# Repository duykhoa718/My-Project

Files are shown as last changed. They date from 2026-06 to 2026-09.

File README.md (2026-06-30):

This is the workplace for designing a buck converter with 6.8V and 20A current max.
This circuit is used for serving the 12 servo Miuzel 20kg torque with a current load from 1-2A 
The purpose of using 12 servos is to design a 12 servo with enough power supply and connect it to the Jetson Orin Nano to control the movement
The input power source is only designed for a 5s LiPo battery.

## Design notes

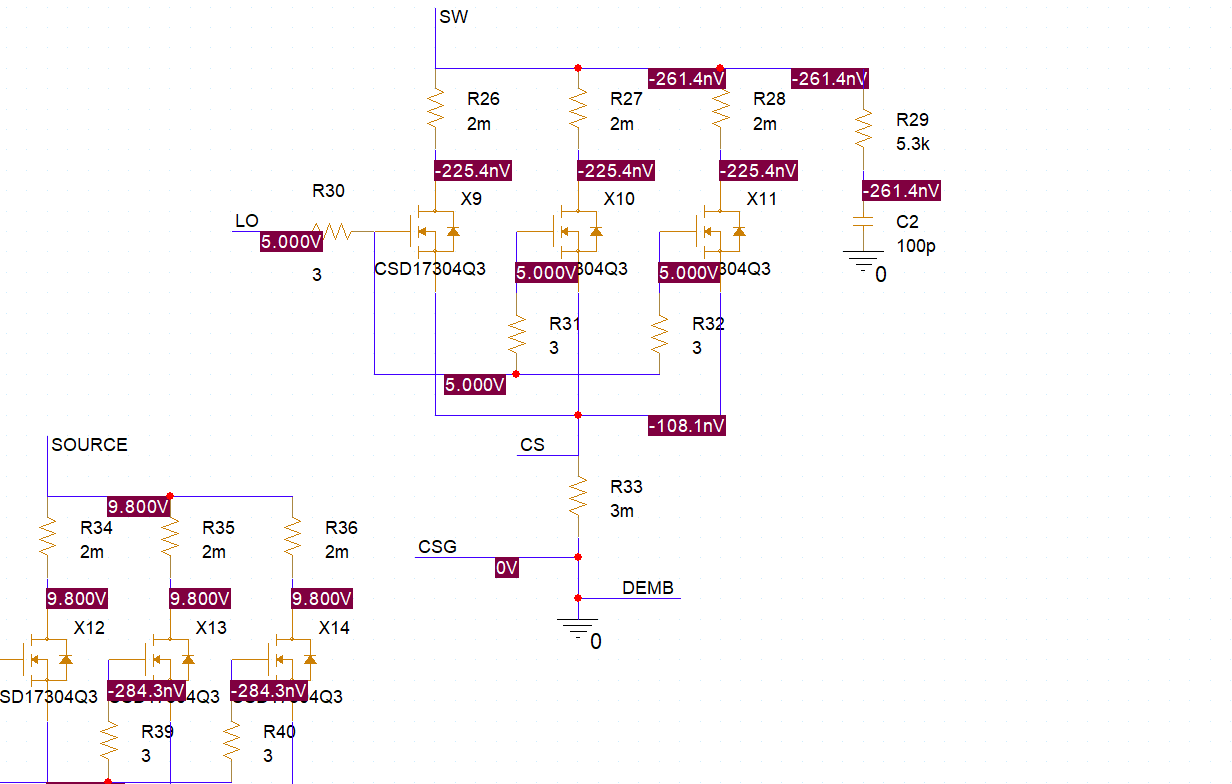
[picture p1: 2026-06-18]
Ai Sipder Bot Power System/PSpice And LTspice For Ti LM5116 Design Schematic/LM5116/LM5116.png

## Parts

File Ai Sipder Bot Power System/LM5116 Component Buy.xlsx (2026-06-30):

DigiKey - Shopping Cart
Index | Quantity | Part Number | Manufacturer Part Number | Description | Customer Reference | Available | Backorder | Unit Price | Extended Price USD
1 | 2 | 1276-1040-1-ND | CL10A225KO8NNNC | CAP CER 2.2UF 16V X5R 0603 |  | 2 | 0 | 0.1 | 0.20
2 | 10 | 296-27509-1-ND | CSD17304Q3 | MOSFET N-CH 30V 15A/56A 8VSON |  | 10 | 0 | 0.935 | 9.35
3 | 1 | 296-40599-1-ND | TLV1701AIDBVR | IC COMPARATOR 1 GEN PUR SOT23-5 |  | 1 | 0 | 1.16 | 1.16
4 | 1 | 5399-TL431CT-ND | TL431 | 2.5V~36V 2% 37V 100MA ADJUSTABLE |  | 1 | 0 | 0.1 | 0.10
5 | 10 | 1N5819HW-FDICT-ND | 1N5819HW-7-F | DIODE SCHOTTKY 40V 1A SOD123 |  | 10 | 0 | 0.178 | 1.78
6 | 10 | 490-14514-1-ND | GCM155R71H104KE02J | CAP CER 0.1UF 50V X7R 0402 |  | 10 | 0 | 0.034 | 0.34
7 | 1 | 399-C0603C824K4PACTUCT-ND | C0603C824K4PACTU | CAP CER 0.82UF 16V X5R 0603 |  | 1 | 0 | 0.26 | 0.26
8 | 1 | 399-A768EB107M1ELAS036CT-ND | A768EB107M1ELAS036 | CAP ALUM POLY 100UF 20% 25V SMD |  | 1 | 0 | 0.55 | 0.55
9 | 10 | 490-6113-1-ND | GRM0335C1H101JA01D | CAP CER 100PF 50V C0G/NP0 0201 |  | 10 | 0 | 0.014 | 0.14
10 | 2 | 553-3446-1-ND | PA4343.142NLT | FIXED IND 1.4UH 27A 2.6 MOHM SMD |  | 2 | 0 | 1.69 | 3.38
11 | 1 | 311-1.21KHRCT-ND | RC0603FR-071K21L | RES 1.21K OHM 1% 1/10W 0603 |  | 1 | 0 | 0.1 | 0.10
12 | 1 | 2019-RN73R1ETTP4811B25CT-ND | RN73R1ETTP4811B25 | RES 4.81K OHM 0.1% 1/16W 0402 |  | 1 | 0 | 0.1 | 0.10
13 | 1 | 311-226KHRCT-ND | RC0603FR-07226KL | RES 226K OHM 1% 1/10W 0603 |  | 1 | 0 | 0.1 | 0.10
14 | 1 | 490-6186-1-ND | GRM1555C1H100FA01D | CAP CER 10PF 50V C0G/NP0 0402 |  | 1 | 0 | 0.1 | 0.10
15 | 10 | 311-0.0JRCT-ND | RC0402JR-070RL | RES 0 OHM JUMPER 1/16W 0402 |  | 10 | 0 | 0.01 | 0.10
16 | 1 | 296-LM5155QDSSTQ1CT-ND | LM5155QDSSTQ1 | POWER MANAGEMENT |  | 1 | 0 | 3.6 | 3.60
17 | 1 | 296-TPS552892RYQRCT-ND | TPS552892RYQR | IC REG BUCK BOOST PROG 5A 21VQFN |  | 1 | 0 | 7.21 | 7.21
18 | 10 | 13-RC0402FR-073RLCT-ND | RC0402FR-073RL | RES 3 OHM 1% 1/16W 0402 |  | 10 | 0 | 0.026 | 0.26
19 | 1 | 1727-8643-1-ND | 2N7002NXAKR | MOSFET N-CH 60V 190MA TO236AB |  | 1 | 0 | 0.14 | 0.14
20 | 10 | 311-1.00MLRCT-ND | RC0402FR-071ML | RES 1M OHM 1% 1/16W 0402 |  | 10 | 0 | 0.021 | 0.21
21 | 10 | 399-C0603C105K4RACTUCT-ND | C0603C105K4RACTU | CAP CER 1UF 16V X7R 0603 |  | 10 | 0 | 0.054 | 0.54
22 | 1 | 2019-RN73R1JTTD5301B25CT-ND | RN73R1JTTD5301B25 | RES 5.3K OHM 0.1% 1/10W 0603 |  | 1 | 0 | 0.1 | 0.10
23 | 2 | 2019-RN73R1ETTP5831B25CT-ND | RN73R1ETTP5831B25 | RES 5.83K OHM 0.1% 1/16W 0402 |  | 2 | 0 | 0.1 | 0.20
24 | 5 | 5923-0678H9300-02CT-ND | 0678H9300-02 | FUSE BRD MT 30A 250VAC 125VDC |  | 5 | 0 | 1.026 | 5.13
25 | 1 | 1276-1244-1-ND | CL21A475KAQNNNE | CAP CER 4.7UF 25V X5R 0805 |  | 1 | 0 | 0.11 | 0.11
26 | 4 | 399-A768MS157M1HLAE024CT-ND | A768MS157M1HLAE024 | CAP ALUM POLY 150UF 20% 50V SMD |  | 4 | 0 | 1.14 | 4.56
27 | 1 | 311-2KLRCT-ND | RC0402FR-072KL | RES 2K OHM 1% 1/16W 0402 |  | 1 | 0 | 0.1 | 0.10
28 | 1 | P140HCT-ND | ERJ-3EKF1400V | RES SMD 140 OHM 1% 1/10W 0603 |  | 1 | 0 | 0.1 | 0.10
29 | 1 | 846-SML-D12U8WT86CT-ND | SML-D12U8WT86 | LED RED DIFFUSED 0603 SMD |  | 1 | 0 | 0.2 | 0.20
30 | 1 | 448-IQDH29NE2LM5CGATMA1CT-ND | IQDH29NE2LM5CGATMA1 | OPTIMOS 6 POWER-TRANSISTOR |  | 1 | 0 | 3.75 | 3.75
31 | 1 | 738-CSSU2512FT3L00CT-ND | CSSU2512FT3L00 | RES SHUNT, 2512, 0.003 OHM, 1%, |  | 1 | 0 | 1.14 | 1.14
32 | 1 | RG16P5.6KBCT-ND | RG1608P-562-B-T5 | RES SMD 5.6K OHM 0.1% 1/10W 0603 |  | 1 | 0 | 0.11 | 0.11
33 | 12 | 732-5316-ND | 61300311121 | CONN HEADER VERT 3POS 2.54MM |  | 12 | 0 | 0.113 | 1.36
34 | 12 | 2057-PH1-01-UA-ND | PH1-01-UA | CONN HEADER VERT 1POS 2.54MM |  | 12 | 0 | 0.029 | 0.35
35 | 1 | LM5116MHX/NOPBCT-ND | LM5116MHX/NOPB | IC REG CTRLR BUCK 20TSSOP |  | 1 | 0 | 6.35 | 6.35
36 | 1 | EG2355-ND | 100SP1T1B4M2QE | SWITCH TOGGLE SPDT 5A 120V |  | 1 | 0 | 2.93 | 2.93
37 | 1 | 399-A783MW687M1VLAS011CT-ND | A783MW687M1VLAS011 | CAP ALU HYBRID 125C 35V 680UF |  | 1 | 0 | 1.86 | 1.86
38 | 1 | 445-5599-1-ND | CGA2B2C0G1H181J050BA | CAP CER 180PF 50V C0G 0402 |  | 1 | 0 | 0.1 | 0.10
39 | 1 | 478-KGM21NR71H333JTCT-ND | KGM21NR71H333JT | CAP CER 0.033UF 50V X7R 0805 |  | 1 | 0 | 0.21 | 0.21
40 | 1 | 541-22.6KLCT-ND | CRCW040222K6FKED | RES 22.6K OHM 1% 1/16W 0402 |  | 1 | 0 | 0.1 | 0.10
41 | 1 | P2.49KDBCT-ND | ERA-3AEB2491V | RES SMD 2.49KOHM 0.1% 1/10W 0603 |  | 1 | 0 | 0.1 | 0.10

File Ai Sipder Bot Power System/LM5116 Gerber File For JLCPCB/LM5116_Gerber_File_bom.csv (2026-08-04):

Designator | Footprint | Quantity | Value | LCSC Part #
C10, C6, C7 | 0603 | 3 | 1u
C11, C14 | CP_Radial_D10.0mm_P5.00mm | 2 | 2200u
C15, C16, C17, C18, C22, C23, C24 | 0603 | 7 | 2.2u
C19, C21, C8 | 0603 | 3 | 100p
C2 | 0603 | 1 | 180p
C20 | 0603 | 1 | 10p
C3 | 1206 | 1 | 33n
C4 | CP_Radial_D10.0mm_P5.00mm | 1 | 1000u
C5 | 0805 | 1 | 4.7u
C9 | 0603 | 1 | 820n
CR1 | CR_LT27A-7_DIO | 1 | DFLT27A-7
CR2 | SMB_DIO | 1 | SMBJ7.0CA-13-F
D1, D2, D3 | SOD3715X145N | 3 | 1N5819HW-7-F
D4 | 0603 | 1 | LED
F1 | FUSC9830X318N | 1 | 0678H9300-02
J1, J10, J11, J12, J2, J3, J4, J5, J6, J7, J8, J9 | WURTH_61300411121 | 12 | 61300411121
J14 | AMASS_XT60-M | 1 | XT60-M
J15 | CUI_TB002V-500-02BE | 1 | TB002V-500-02BE
L1, L2 | L_Pulse_PA4341 | 2 | 1.38u
Q1, Q2, Q3, Q4 | DQG0008A | 4 | CSD17304Q3
Q5 | SOT-23_Handsoldering | 1 | 2N7002
Q6 | IFX-PG-TTFN-9-2-V | 1 | IQDH29NE2LM5CG
R1 | 0402 | 1 | 0
R10 | 0603 | 1 | 226k
R11, R12, R14, R15 | 0603 | 4 | 3
R13, R22 | 0603 | 2 | 5.83k
R17 | 2512 | 1 | 3m
R19, R21, R23, R24, R25, R26, R27 | 0603 | 7 | 10k
R2 | 0805 | 1 | 22.6k
R20 | 0805 | 1 | 4.81k
R3 | 0805 | 1 | 2.49k
R4 | 0402 | 1 | 1Meg
R5 | 0603 | 1 | 5.3k
R6 | 0603 | 1 | 330
R7 | 0603 | 1 | 2k
R8 | 0603 | 1 | 5.6k
R9 | 0603 | 1 | 1.21k
SW1 | SW_1218_EWI | 1 | EG1218
U1 | MXA20A_TEX-M | 1 | LM25116MHX/NOPB
U2 | SOT95P280X145-5N | 1 | TLV1701AIDBVR
U3 | SOT-23_Handsoldering | 1 | TL431DBZ

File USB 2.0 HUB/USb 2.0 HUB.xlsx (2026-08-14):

DigiKey - Shopping Cart
Index | Quantity | Part Number | Manufacturer Part Number | Description | Unit of Measure | Customer Reference | Available | Backorder | Unit Price | Extended Price USD
1 | 1 | USB2512BT/M2CT-ND | USB2512BT/M2 | IC HUB CTLR 2PORT USB 2.0 HS 36S |  |  | 1 | 0 | 1.9 | 1.90
2 | 2 | 2057-USB-A-S-VT-ND | USB-A-S-VT | USB TYPE A SINGLE VERTICAL |  |  | 2 | 0 | 0.48 | 0.96
3 | 1 | 2073-USB4110-GF-A-1-ND | USB4110-GF-A | CONN RCP USB2.0 TYP C 24P SMD RA |  |  | 1 | 0 | 1.27 | 1.27
4 | 1 | SER3635CT-ND | TSX-3225 24.0000MF15X-AC3 | CRYSTAL 24.0000MHZ 9PF SMD |  |  | 1 | 0 | 0.87 | 0.87
5 | 2 | 490-3113-1-ND | GJM1555C1H100JB01D | CAP CER 10PF 50V C0G/NP0 0402 |  |  | 2 | 0 | 0.13 | 0.26
6 | 10 | 1934-1472-1-ND | 2508051217Y6 | FERRITE BEAD 120 OHM 0805 1LN |  |  | 10 | 0 | 0.092 | 0.92
7 | 1 | AZ1117CH-3.3TRG1DICT-ND | AZ1117CH-3.3TRG1 | IC REG LINEAR 3.3V 1A SOT-223-3 |  |  | 1 | 0 | 0.19 | 0.19
8 | 1 | 296-31979-1-ND | TPS2064DGNR | IC PWR SWITCH N-CHAN 1:2 8MSOP |  |  | 1 | 0 | 2.45 | 2.45
9 | 3 | NUP4114UPXV6T2GOSCT-ND | NUP4114UPXV6T2G | TVS DIODE 5.5VWM 10VC SOT563 |  |  | 3 | 0 | 0.88 | 2.64
10 | 10 | 311-634HRCT-ND | RC0603FR-07634RL | RES 634 OHM 1% 1/10W 0603 |  |  | 10 | 0 | 0.025 | 0.25
11 | 10 | 541-1.00KHCT-ND | CRCW06031K00FKEA | RES SMD 1K OHM 1% 1/8W 0603 |  |  | 10 | 0 | 0.032 | 0.32
12 | 10 | 541-100KHCT-ND | CRCW0603100KFKEA | RES SMD 100K OHM 1% 1/8W 0603 |  |  | 10 | 0 | 0.032 | 0.32
13 | 10 | 311-5.10KHRCT-ND | RC0603FR-075K1L | RES 5.1K OHM 1% 1/10W 0603 |  |  | 10 | 0 | 0.027 | 0.27
14 | 10 | 311-12.0KHRCT-ND | RC0603FR-0712KL | RES 12K OHM 1% 1/10W 0603 |  |  | 10 | 0 | 0.025 | 0.25
15 | 10 | 399-C0603C100J5GACTUCT-ND | C0603C100J5GACTU | CAP CER 10PF 50V C0G/NP0 0603 |  |  | 10 | 0 | 0.091 | 0.91
16 | 1 | 1276-1065-1-ND | CL21A475KOFNNNE | CAP CER 4.7UF 16V X5R 0805 |  |  | 1 | 0 | 0.11 | 0.11
17 | 1 | 587-3246-1-ND | TMK316BBJ226ML-T | CAP CER 22UF 25V X5R 1206 |  |  | 1 | 0 | 0.44 | 0.44
18 | 2 | 399-A768MS157M1HLAE024CT-ND | A768MS157M1HLAE024 | CAP ALUM POLY 150UF 20% 50V SMD |  |  | 2 | 0 | 1.17 | 2.34
19 | 20 | 445-7456-1-ND | C1608X5R1H104K080AA | CAP CER 0.1UF 50V X5R 0603 |  |  | 20 | 0 | 0.057 | 1.14
20 | 3 | 160-1423-1-ND | LTST-C171GKT | LED GREEN CLEAR CHIP SMD |  |  | 3 | 0 | 0.15 | 0.45
21 | 10 | 399-C0402C103K5RACTUCT-ND | C0402C103K5RACTU | CAP CER 10000PF 50V X7R 0402 |  |  | 10 | 0 | 0.037 | 0.37

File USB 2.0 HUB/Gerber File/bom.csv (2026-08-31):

Designator | Footprint | Quantity | Value | LCSC Part #
C1, C2 | 0402 | 2 | 10p
C10, C4 | 0805 | 2 | 4.7u
C11, C13, C14, C5, C6, C8 | 0805 | 6 | 0.1u
C12 | 1206 | 1 | 22u
C15, C3 | 0603 | 2 | 2.2u
C16 | 0603 | 1 | 1u
C17, C18, C19, C20, C23, C24 | 0603 | 6 | 0.1u
C21, C22 | 0402 | 2 | 10n
C7, C9 | CAP_A768MS_KEM | 2 | 150u
D1, D2, D3 | 0805 | 3 | LED
D4, D5, D6 | SOT95P275X110-6N | 3 | NUP4114HMR6T1G
J1, J2 | CONN_USB-A-S-VT_ADM | 2 | USB-A-S-VT
J3 | GCT_USB4110GFA | 1 | USB4110GFA
L1, L2 | IND_25_0805_FRT | 2 | 2508051217Y6
R1 | 0603 | 1 | 634
R10, R7, R8, R9 | 0603 | 4 | 330
R11, R12, R14, R15, R18, R19, R3, R4 | 0603 | 8 | 100k
R13 | 0402 | 1 | NP_1M
R16 | 0603 | 1 | 12k
R2 | 0603 | 1 | 1k
R5, R6 | 0603 | 2 | 5.1k
U1 | 36SQFN-3706-6X6B_MCH | 1 | USB2512BT/M2
U3 | SOT-223_DIO | 1 | AZ1117CH-3.3TRG1
U4 | DGN8_1P89X1P57 | 1 | TPS2064DGNR
Y1 | OSCCC320X250X60 | 1 | TSX-322524.0000MF15X-AC3

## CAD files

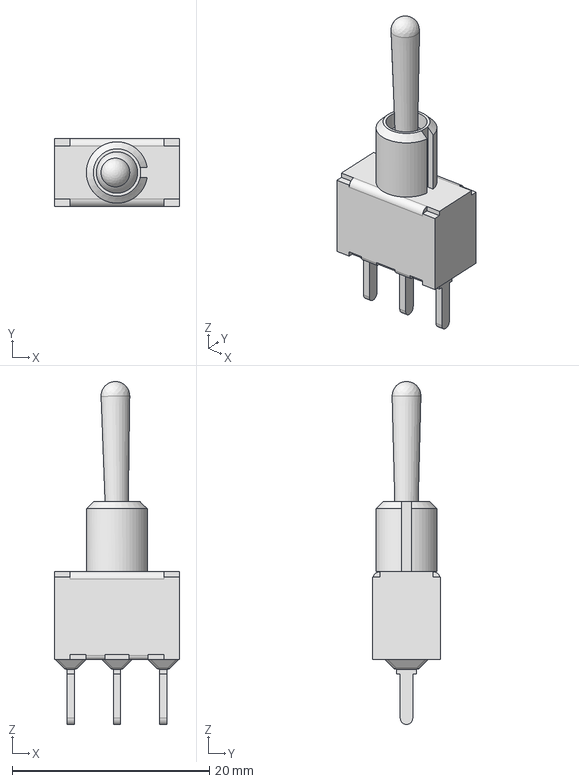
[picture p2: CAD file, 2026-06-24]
Ai Sipder Bot Power System/LM5116 Component File/100SP1T1B4M2QE/100SP1T1B4M2QE.step
12.7 x 6.86 x 34.8 mm

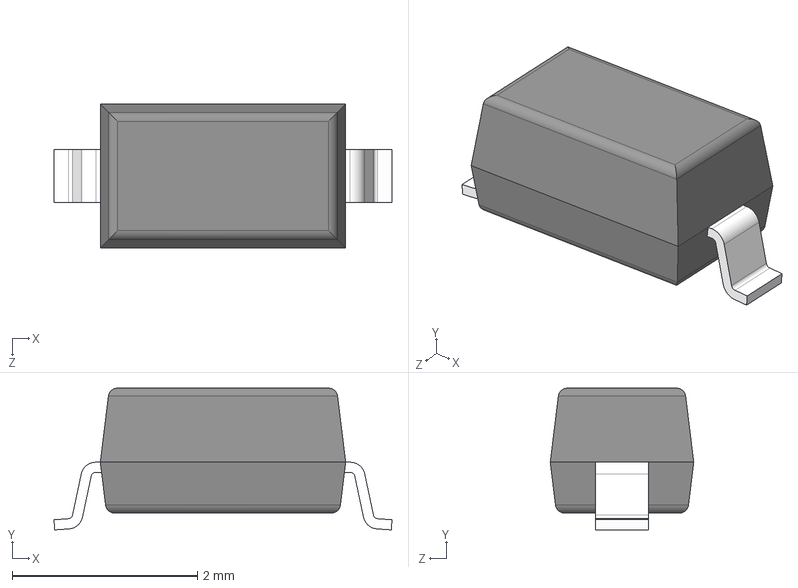
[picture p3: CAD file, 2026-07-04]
Ai Sipder Bot Power System/LM5116 Component File/1N5819HW_7_F/1N5819HW-7-F.step
3.65 x 1.53 x 1.55 mm

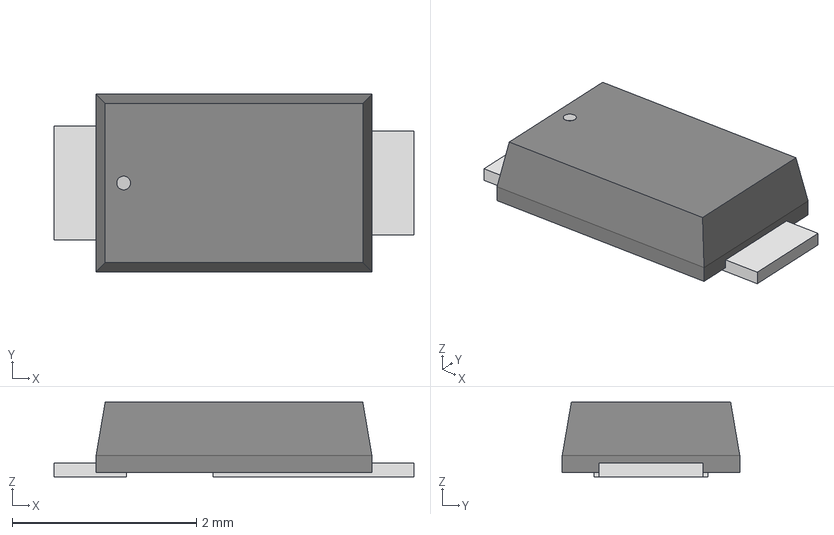
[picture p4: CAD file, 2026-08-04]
Ai Sipder Bot Power System/LM5116 Component File/DFLT27A_7/CR_LT27A-7_DIO.step
3.91 x 1.93 x 0.815 mm

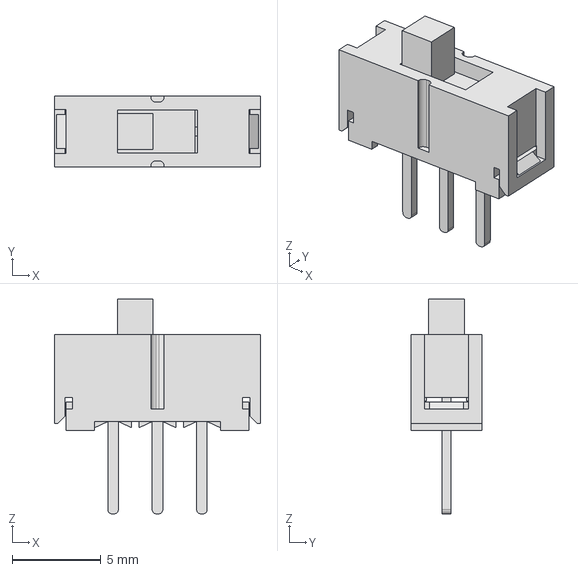
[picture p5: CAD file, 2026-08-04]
Ai Sipder Bot Power System/LM5116 Component File/EG1218/KiCADv6/EG1218.STEP
11.6 x 4.00 x 12.1 mm

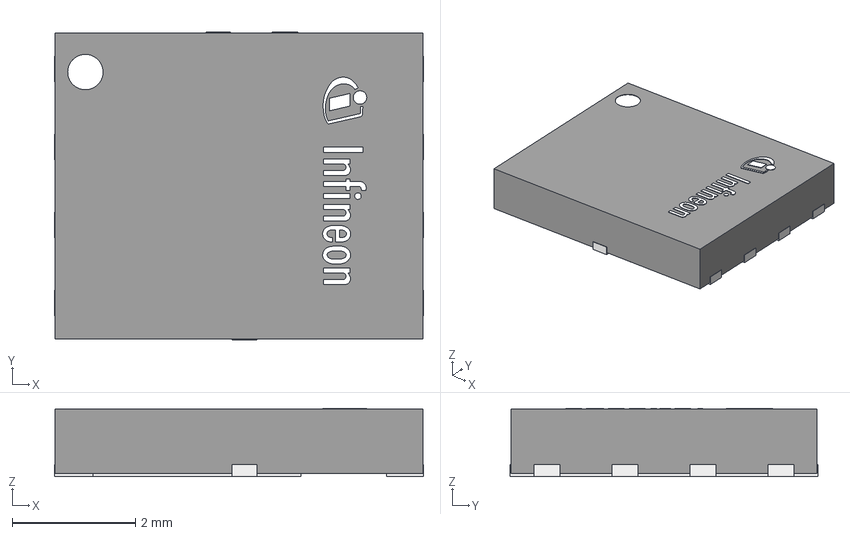
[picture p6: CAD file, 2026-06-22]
Ai Sipder Bot Power System/LM5116 Component File/IQDH29NE2LM5CGATMA1/PG-TTFN-9-2_Z8B00203958_V01_3D.stp
6.00 x 5.00 x 1.11 mm

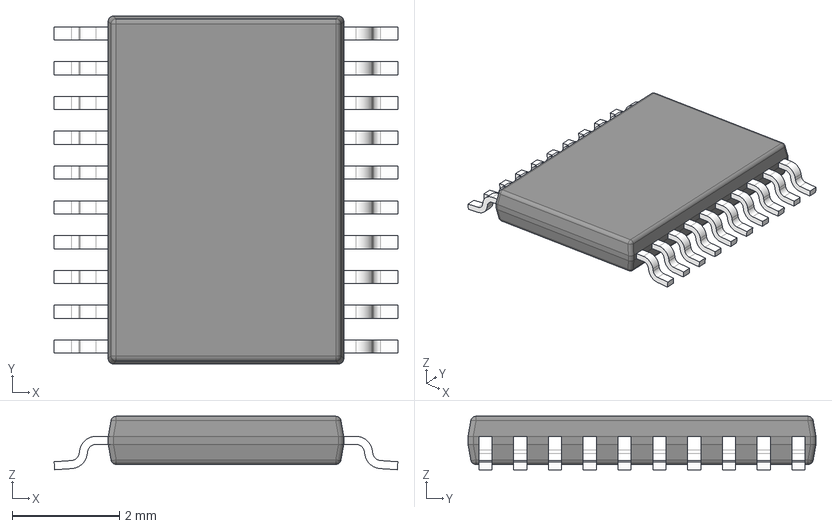
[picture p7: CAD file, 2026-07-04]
Ai Sipder Bot Power System/LM5116 Component File/LM25116MHX_NOPB/PWP0020A.stp
6.42 x 6.50 x 1.00 mm
BODY-SO
LEAD-SO x 20
THERMALPAD-SO
PIN1-ID

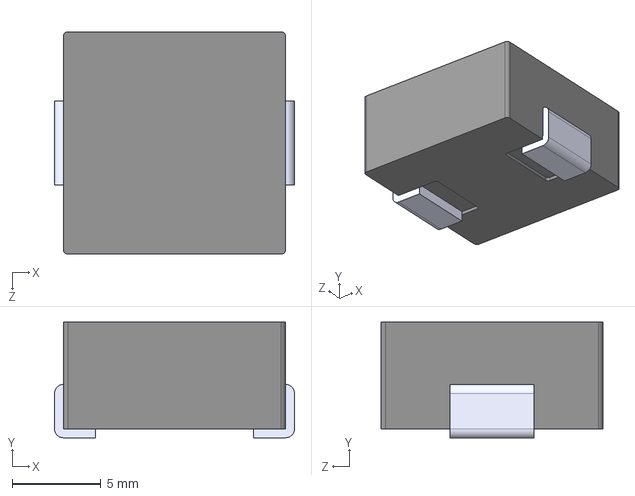
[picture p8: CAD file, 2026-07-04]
Ai Sipder Bot Power System/LM5116 Component File/PA4343_142NLT/PA4343.142NLT.STEP
13.5 x 6.50 x 12.5 mm

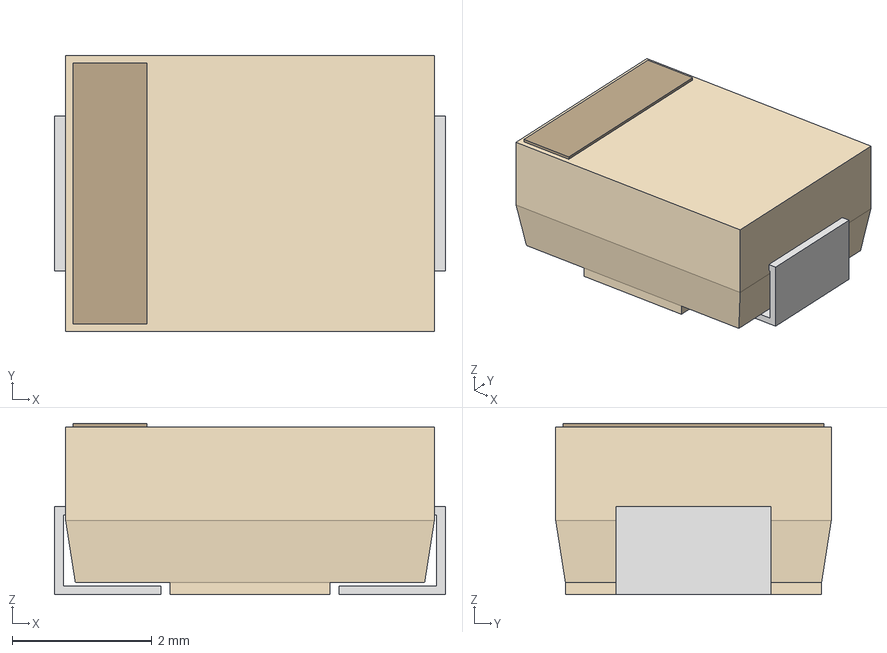
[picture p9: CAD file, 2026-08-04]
Ai Sipder Bot Power System/LM5116 Component File/SMBJ7_0CA_13_F/SMB_DIO.step
5.59 x 3.94 x 2.45 mm

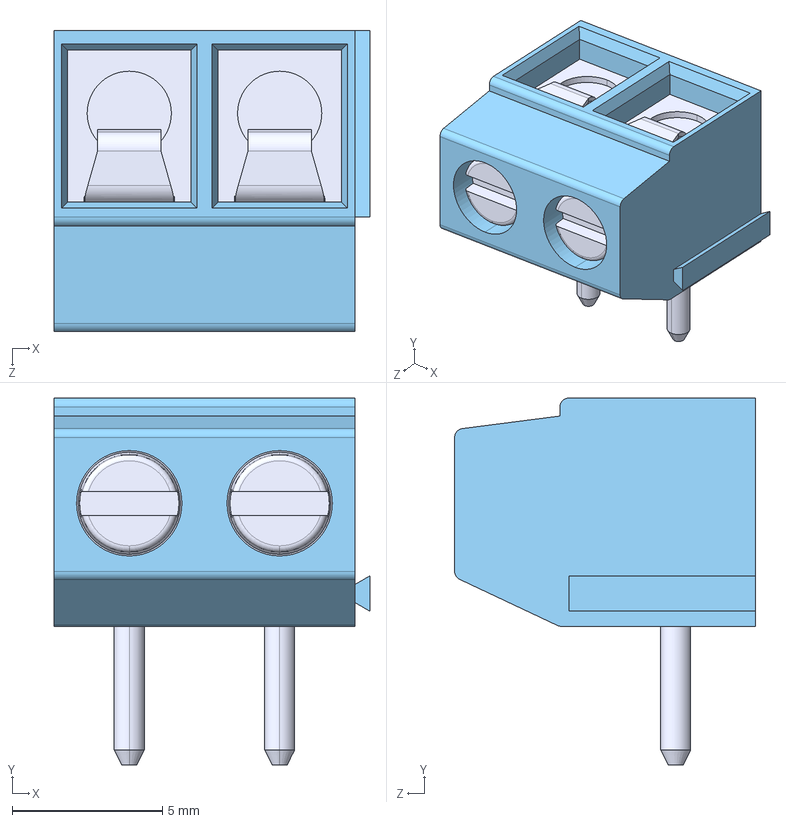
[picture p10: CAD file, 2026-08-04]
Ai Sipder Bot Power System/LM5116 Component File/TB002V_500_02BE (1)/TB002V-500-02BE.step
10.5 x 12.2 x 10.0 mm

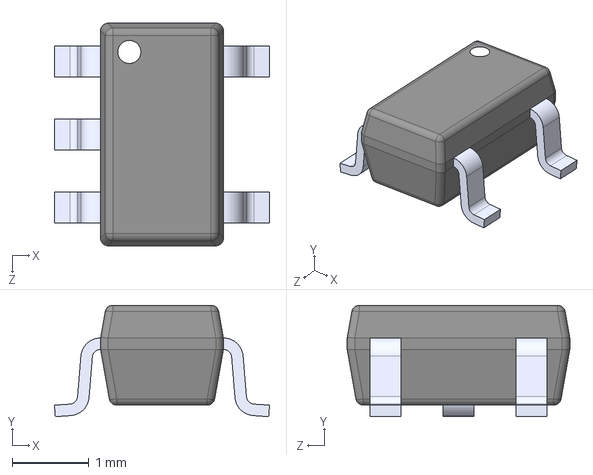
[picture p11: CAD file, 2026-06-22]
Ai Sipder Bot Power System/LM5116 Component File/TLV1701AIDBVR/TLV1701AIDBVR.step
2.80 x 1.45 x 2.90 mm

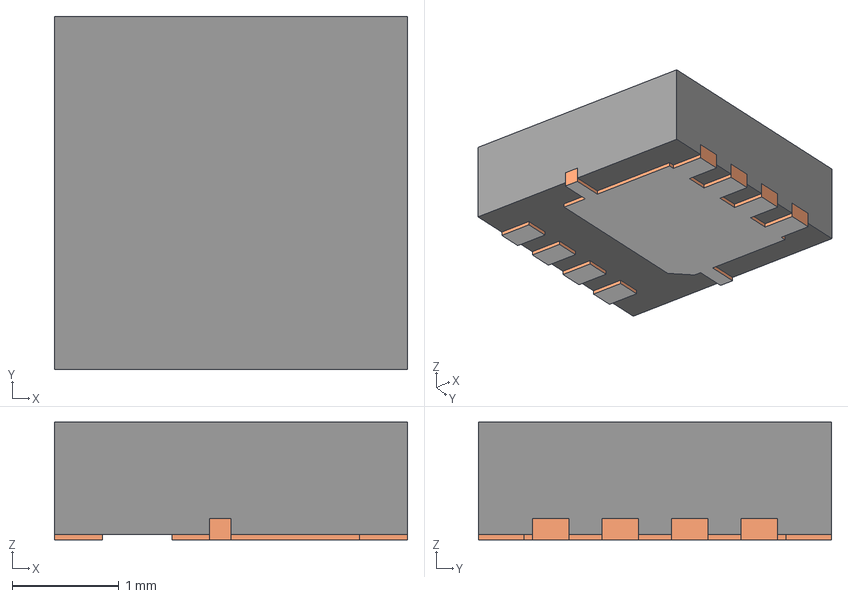
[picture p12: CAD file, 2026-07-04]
Ai Sipder Bot Power System/LM5116 Component File/ul_CSD17304Q3/DQG0008A.stp
3.30 x 3.30 x 1.10 mm
BODY-SON
FRAME-DQG0008A
PIN1-ID

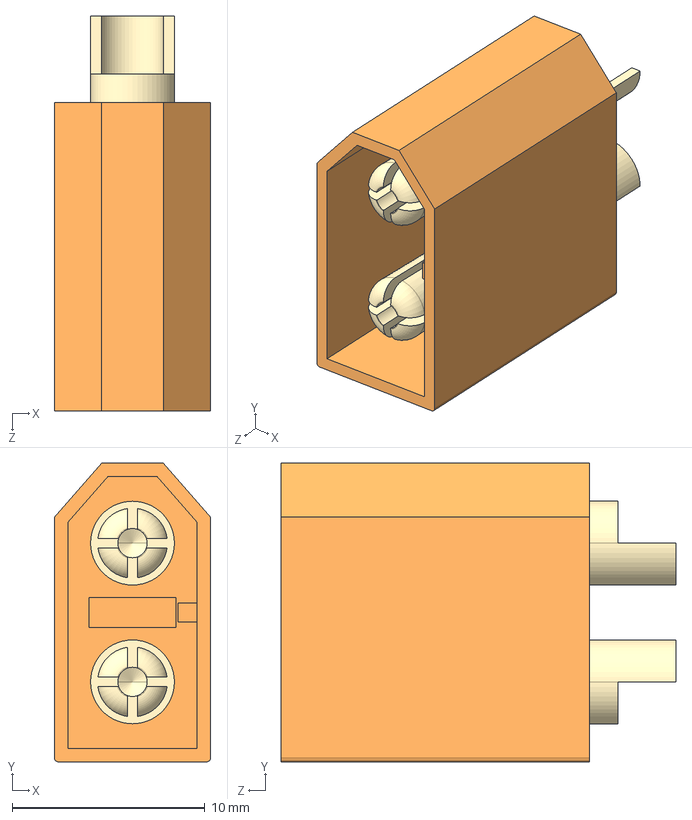
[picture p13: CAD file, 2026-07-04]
Ai Sipder Bot Power System/LM5116 Component File/XT60-M (1)/XT60-M.step
8.10 x 15.5 x 20.5 mm

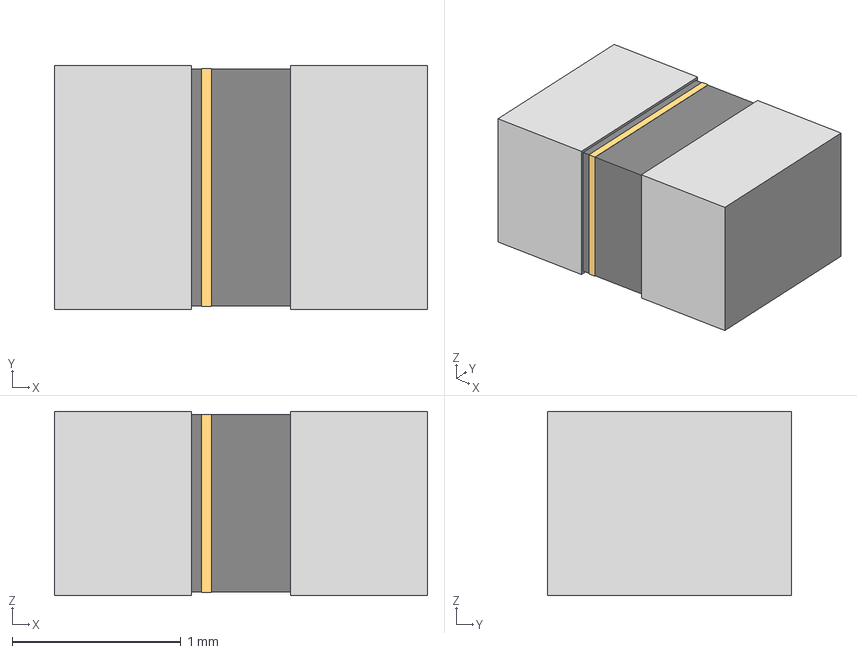
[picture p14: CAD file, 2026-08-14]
USB 2.0 HUB/Component File/2508051217Y6/IND_25_0805_FRT.step
2.21 x 1.45 x 1.09 mm

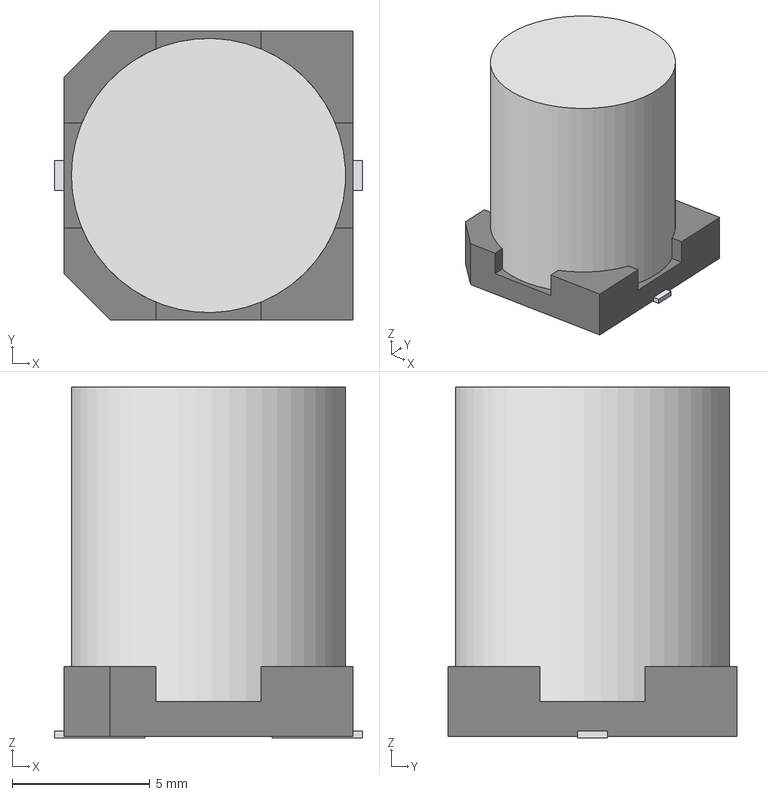
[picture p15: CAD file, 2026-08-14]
USB 2.0 HUB/Component File/A768MS157M1HLAE024/CAP_A768MS_KEM.step
11.2 x 10.5 x 12.8 mm

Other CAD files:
USB 2.0 HUB/Component File/AZ1117CH_3_3TRG1/SOT-223_DIO.step
USB 2.0 HUB/Component File/TPS2064DGNR/DGN0008C.stp
USB 2.0 HUB/Component File/TPS2069DGNR/DGN0008C.stp
USB 2.0 HUB/Component File/TSX_3225_24_0000MF15X_AC3/TSX-322524.0000MF15X-AC3.step
Ai Sipder Bot Power System/LM5116 Component File/0678H9300_02/0678H9300-02.step
Ai Sipder Bot Power System/LM5116 Component File/4 Pin Header/61300411121.step
Ai Sipder Bot Power System/LM5116 Component File/61300311121/61300311121.step
Ai Sipder Bot Power System/LM5116 Component File/691137710002/691137710002.step
USB 2.0 HUB/Component File/USB2512BT_M2/36SQFN-3706-6X6B_MCH.step
USB 2.0 HUB/Component File/USB4110_GF_A/USB4110-GF-A.STEP

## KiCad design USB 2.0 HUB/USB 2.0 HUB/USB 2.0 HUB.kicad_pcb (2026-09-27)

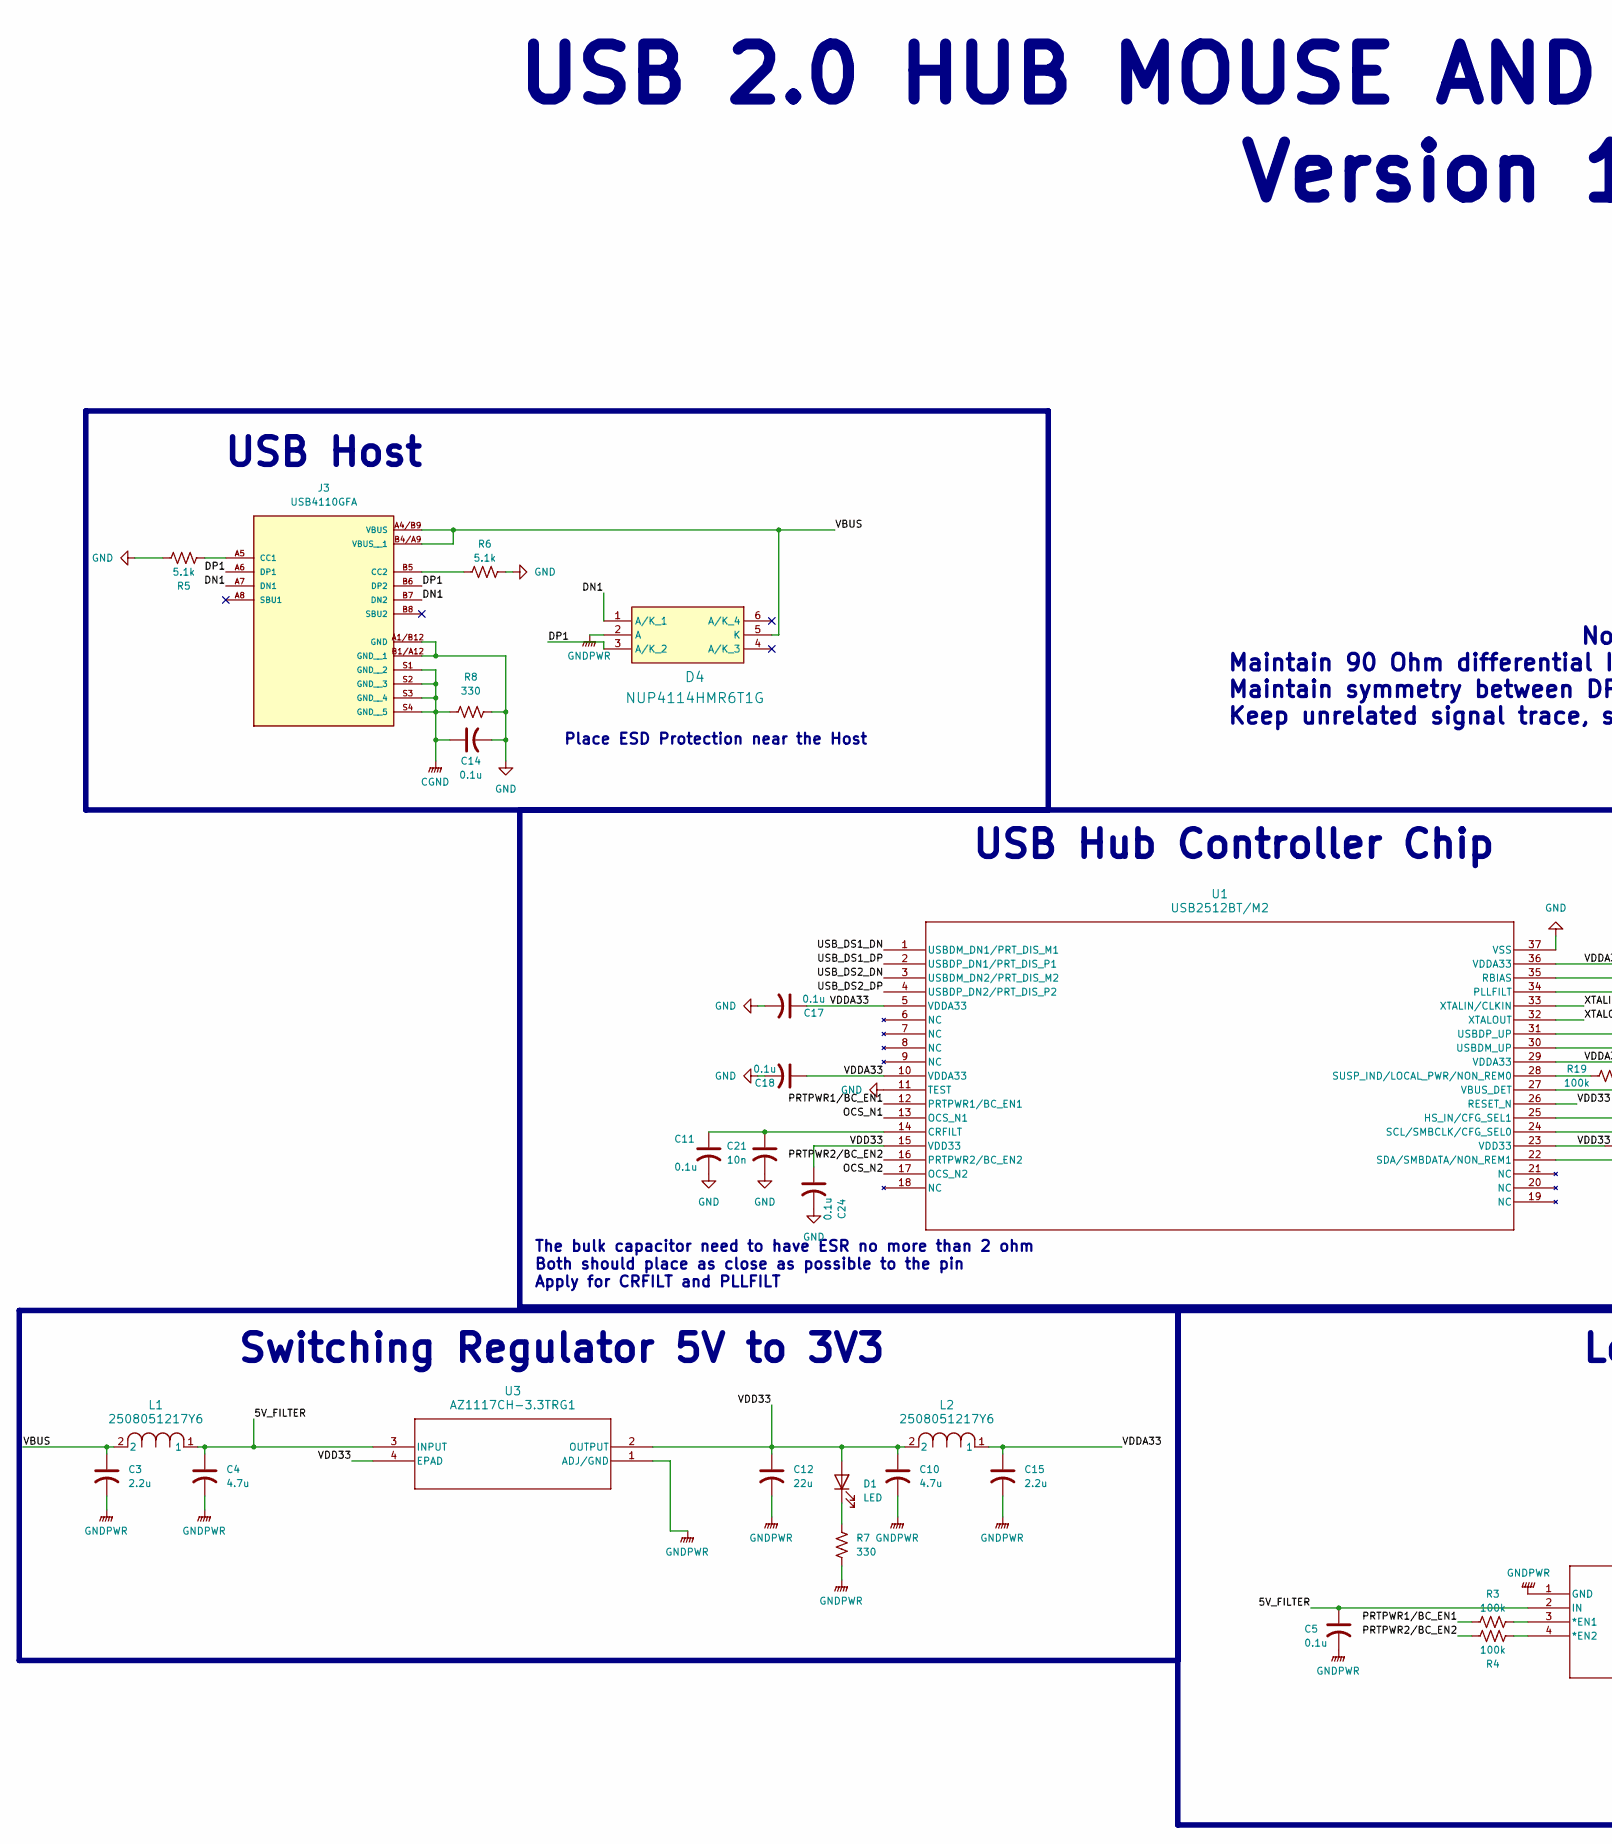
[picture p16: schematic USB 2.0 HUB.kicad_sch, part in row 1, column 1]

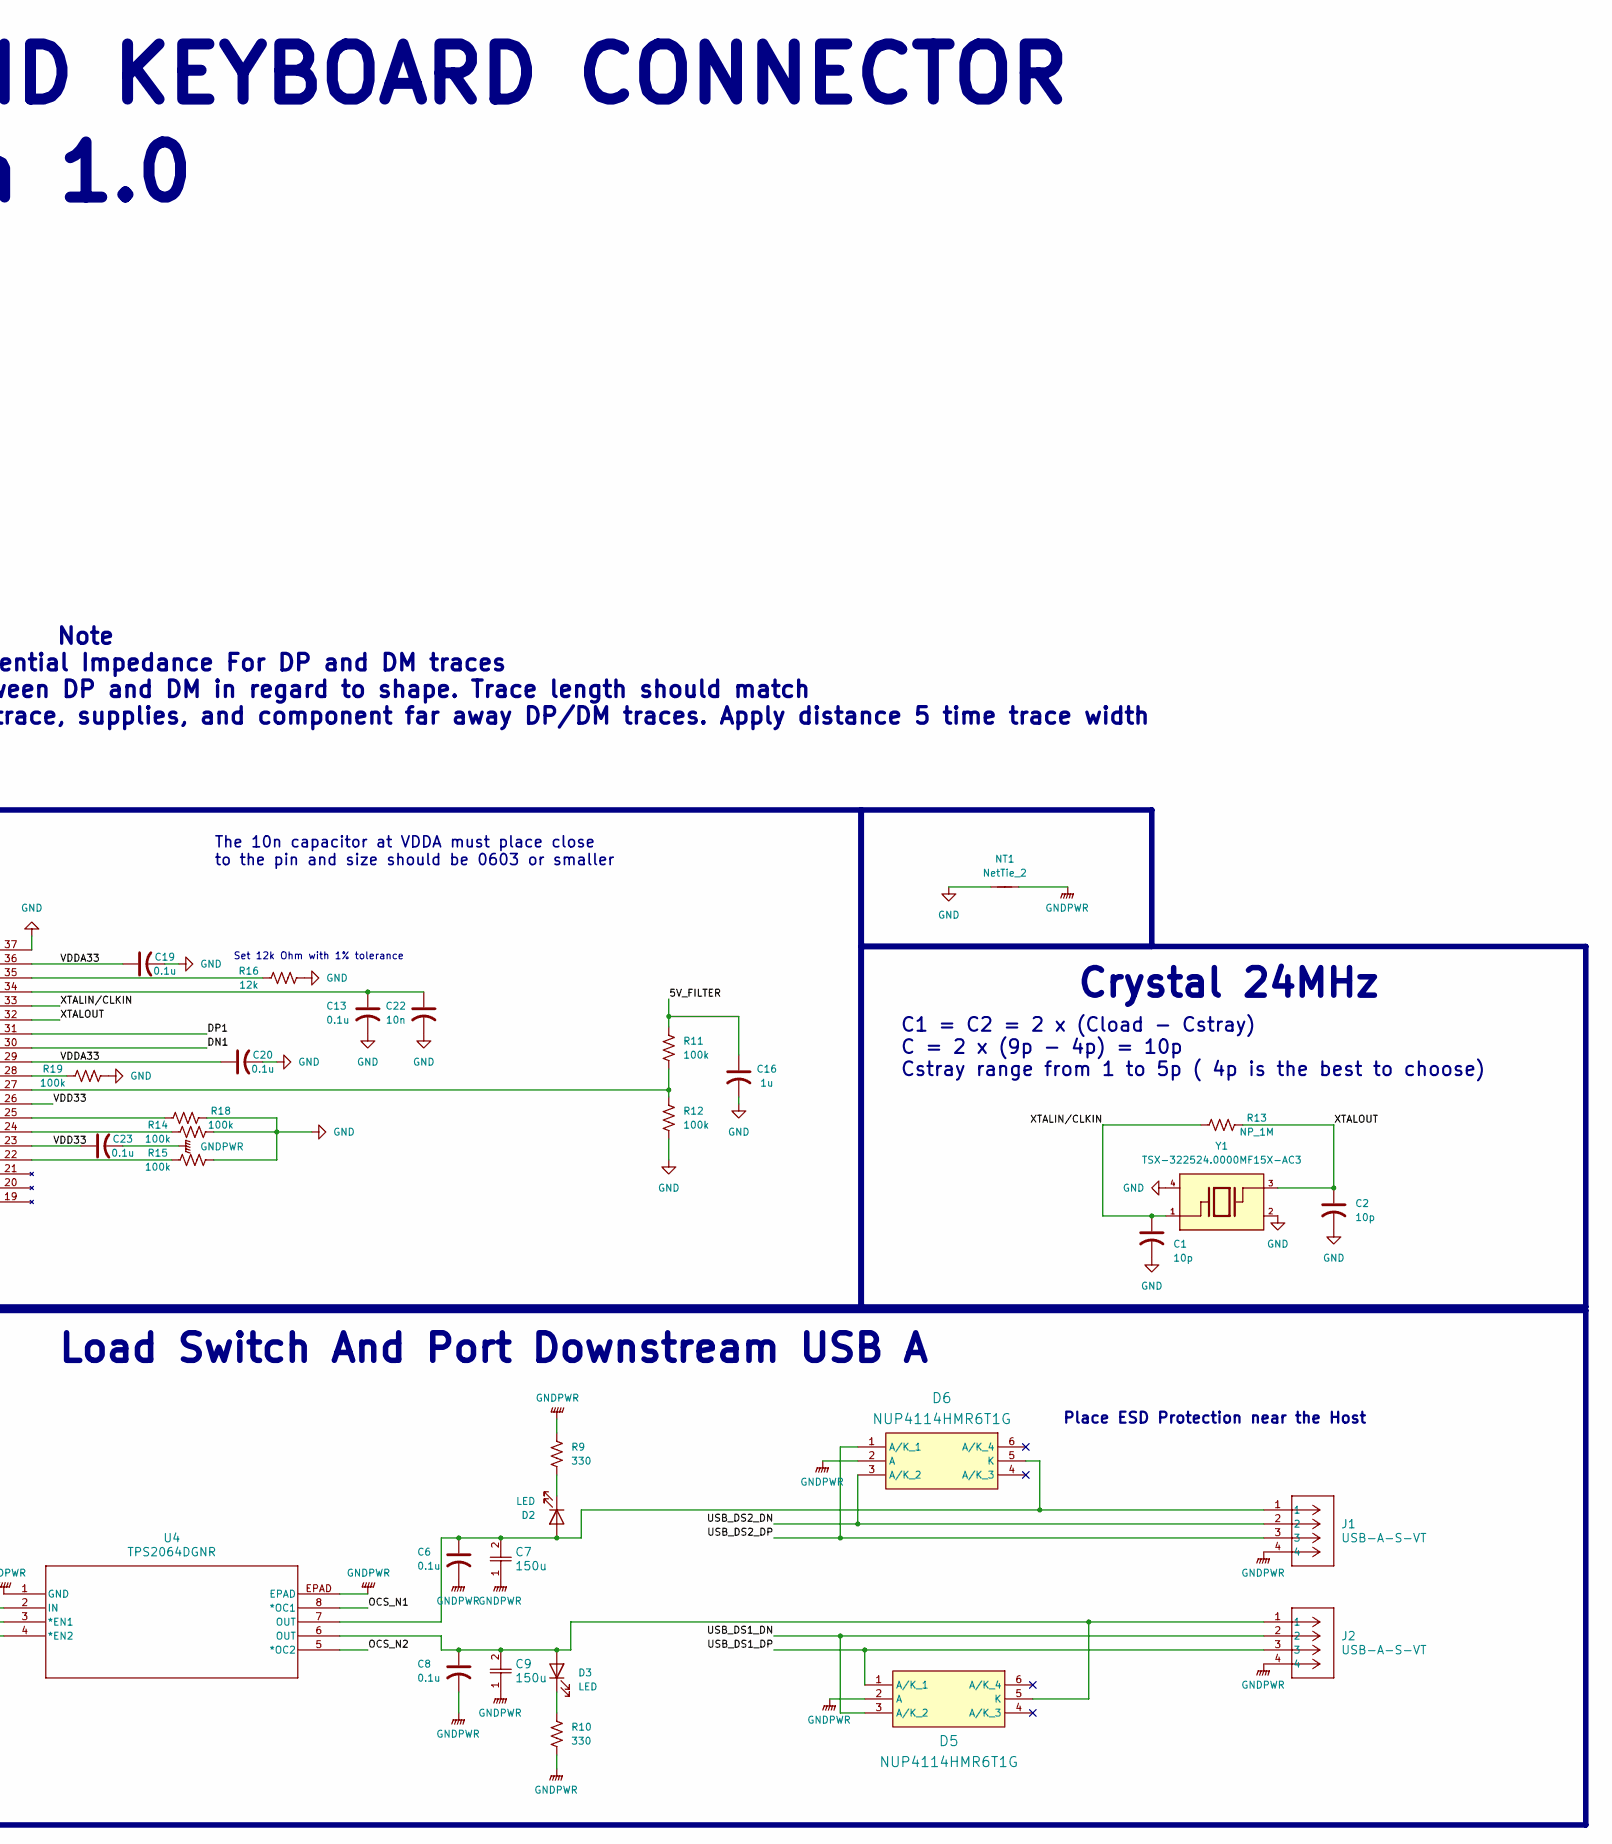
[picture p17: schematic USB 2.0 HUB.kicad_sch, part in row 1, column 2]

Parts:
C1, C2: 10p; C_0402_1005Metric_Pad0.74x0.62mm_HandSolder
C3, C15: 2.2u; C_0603_1608Metric_Pad1.08x0.95mm_HandSolder
C4, C10: 4.7u; C_0805_2012Metric_Pad1.18x1.45mm_HandSolder
C5, C6, C8, C11, C13, C14: 0.1u; C_0805_2012Metric_Pad1.18x1.45mm_HandSolder
C7, C9: 150u; CAP_A768MS_KEM
C12: 22u; C_1206_3216Metric_Pad1.33x1.80mm_HandSolder
C16: 1u; C_0603_1608Metric_Pad1.08x0.95mm_HandSolder
C17, C18, C19, C20, C23, C24: 0.1u; C_0603_1608Metric_Pad1.08x0.95mm_HandSolder
C21, C22: 10n; C_0402_1005Metric_Pad0.74x0.62mm_HandSolder
D1, D2, D3: LED; LED_0805_2012Metric_Pad1.15x1.40mm_HandSolder
D4, D5, D6: NUP4114HMR6T1G; SOT95P275X110-6N; Manufacturer_Part_Number NUP4114HMR6T1G; Mouser Part Number 863-NUP4114HMR6T1G
J1, J2: USB-A-S-VT; CONN_USB-A-S-VT_ADM
J3: USB4110GFA; GCT_USB4110GFA
L1, L2: 2508051217Y6; IND_25_0805_FRT
NT1: NetTie_2; NetTie-2_SMD_Pad0.5mm
R3, R4, R11, R12, R14, R15, R18, R19: 100k; R_0603_1608Metric_Pad0.98x0.95mm_HandSolder
R5, R6: 5.1k; R_0603_1608Metric_Pad0.98x0.95mm_HandSolder
R7, R8, R9, R10: 330; R_0603_1608Metric_Pad0.98x0.95mm_HandSolder
R13: NP_1M; R_0402_1005Metric_Pad0.72x0.64mm_HandSolder
R16: 12k; R_0603_1608Metric_Pad0.98x0.95mm_HandSolder
U1: USB2512BT/M2; 36SQFN-3706-6X6B_MCH
U3: AZ1117CH-3.3TRG1; SOT-223_DIO
U4: TPS2064DGNR; DGN8_1P89X1P57
Y1: TSX-322524.0000MF15X-AC3; OSCCC320X250X60; PARTREV N/A

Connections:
/5V_FILTER: C4.1, C5.1, C16.1, L1.1, R11.2, U3.3 (INPUT), U4.2 (IN)
/DN1: D4.1 (A/K_1), J3.A7 (DN1), J3.B7 (DN2), U1.30 (USBDM_UP)
/DP1: D4.3 (A/K_2), J3.A6 (DP1), J3.B6 (DP2), U1.31 (USBDP_UP)
/OCS_N1: U1.13 (OCS_N1), U4.8 (*OC1)
/OCS_N2: U1.17 (OCS_N2), U4.5 (*OC2)
/PRTPWR1/BC_EN1: R3.1, U1.12 (PRTPWR1/BC_EN1)
/PRTPWR2/BC_EN2: R4.1, U1.16 (PRTPWR2/BC_EN2)
/USB_DS1_DN: D5.3 (A/K_2), J2.2, U1.1 (USBDM_DN1/PRT_DIS_M1)
/USB_DS1_DP: D5.1 (A/K_1), J2.3, U1.2 (USBDP_DN1/PRT_DIS_P1)
/USB_DS2_DN: D6.3 (A/K_2), J1.2, U1.3 (USBDM_DN2/PRT_DIS_M2)
/USB_DS2_DP: D6.1 (A/K_1), J1.3, U1.4 (USBDP_DN2/PRT_DIS_P2)
/VBUS: C3.1, D4.5 (K), J3.A4/B9 (VBUS), J3.B4/A9 (VBUS__1), L1.2
/VDD33: C10.1, C12.1, C23.1, C24.1, D1.2 (A), L2.2, U1.15 (VDD33), U1.23 (VDD33), U1.26 (RESET_N), U3.2 (OUTPUT), U3.4 (EPAD)
/VDDA33: C15.1, C17.1, C18.1, C19.1, C20.1, L2.1, U1.5 (VDDA33), U1.10 (VDDA33), U1.29 (VDDA33), U1.36 (VDDA33)
/XTALIN/CLKIN: C1.1, R13.1, U1.33 (XTALIN/CLKIN), Y1.1
/XTALOUT: C2.1, R13.2, U1.32 (XTALOUT), Y1.3
CGND: C14.1, J3.S1 (GND__2), J3.S2 (GND__3), J3.S3 (GND__4), J3.S4 (GND__5), R8.1
GND: C1.2, C2.2, C11.2, C13.2, C14.2, C16.2, C17.2, C18.2, C19.2, C20.2, C21.2, C22.2, C24.2, J3.A1/B12 (GND), J3.B1/A12 (GND__1), NT1.1, R5.1, R6.1, R8.2, R12.1, R14.1, R15.1, R16.1, R18.1, R19.1, U1.11 (TEST), U1.37 (VSS), Y1.2, Y1.4
GNDPWR: C3.2, C4.2, C5.2, C6.2, C7.1, C8.2, C9.1, C10.2, C12.2, C15.2, C23.2, D4.2 (A), D5.2 (A), D6.2 (A), J1.4, J2.4, NT1.2, R7.2, R9.2, R10.2, U3.1 (ADJ/GND), U4.1 (GND), U4.EPAD
unnamed: D1.1 (K), R7.1
unnamed: C6.1, C7.2, D2.2 (A), D6.5 (K), J1.1, U4.7 (OUT)
unnamed: D2.1 (K), R9.1
unnamed: C8.1, C9.2, D3.2 (A), D5.5 (K), J2.1, U4.6 (OUT)
unnamed: D3.1 (K), R10.1
unnamed: J3.A5 (CC1), R5.2
unnamed: J3.B5 (CC2), R6.2
unnamed: C11.1, C21.1, U1.14 (CRFILT)
unnamed: R18.2, U1.25 (HS_IN/CFG_SEL1)
unnamed: C13.1, C22.1, U1.34 (PLLFILT)
unnamed: R16.2, U1.35 (RBIAS)
unnamed: R14.2, U1.24 (SCL/SMBCLK/CFG_SEL0)
unnamed: R15.2, U1.22 (SDA/SMBDATA/NON_REM1)
unnamed: R19.2, U1.28 (SUSP_IND/LOCAL_PWR/NON_REM0)
unnamed: R11.1, R12.2, U1.27 (VBUS_DET)
unnamed: R3.2, U4.3 (*EN1)
unnamed: R4.2, U4.4 (*EN2)

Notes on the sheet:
Crystal 24MHz
The 10n capacitor at VDDA must place close to the pin and size should be 0603 or smaller
Load Switch And Port Downstream USB A
Version 1.0
Place ESD Protection near the Host
Note Maintain 90 Ohm differential Impedance For DP and DM traces Maintain symmetry between DP and DM in regard to shape. Trace length should match Keep unrelated signal trace, supplies, and component far away DP/DM traces. Apply distance 5 time trace width
USB Host
The bulk capacitor need to have ESR no more than 2 ohm Both should place as close as possible to the pin Apply for CRFILT and PLLFILT
Set 12k Ohm with 1% tolerance
USB 2.0 HUB MOUSE AND KEYBOARD CONNECTOR
C1 = C2 = 2 x (Cload - Cstray) C = 2 x (9p - 4p) = 10p Cstray range from 1 to 5p ( 4p is the best to choose)
Switching Regulator 5V to 3V3
USB Hub Controller Chip

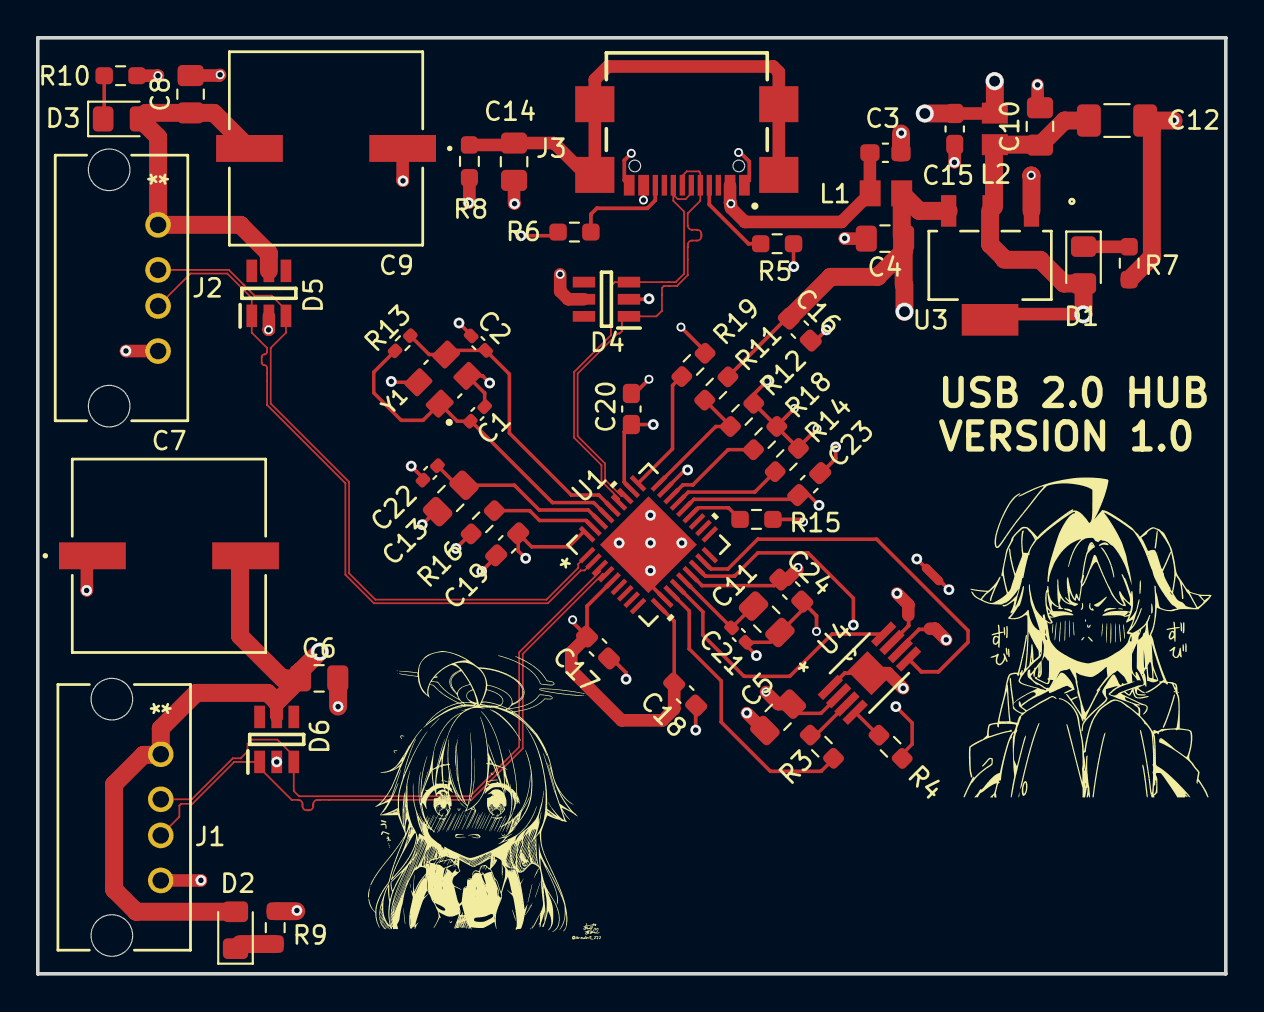
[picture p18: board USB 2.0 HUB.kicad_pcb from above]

Board: 4 copper layers, 66.0 x 52.0 mm, 56 parts (0 on the bottom side), 36 nets.

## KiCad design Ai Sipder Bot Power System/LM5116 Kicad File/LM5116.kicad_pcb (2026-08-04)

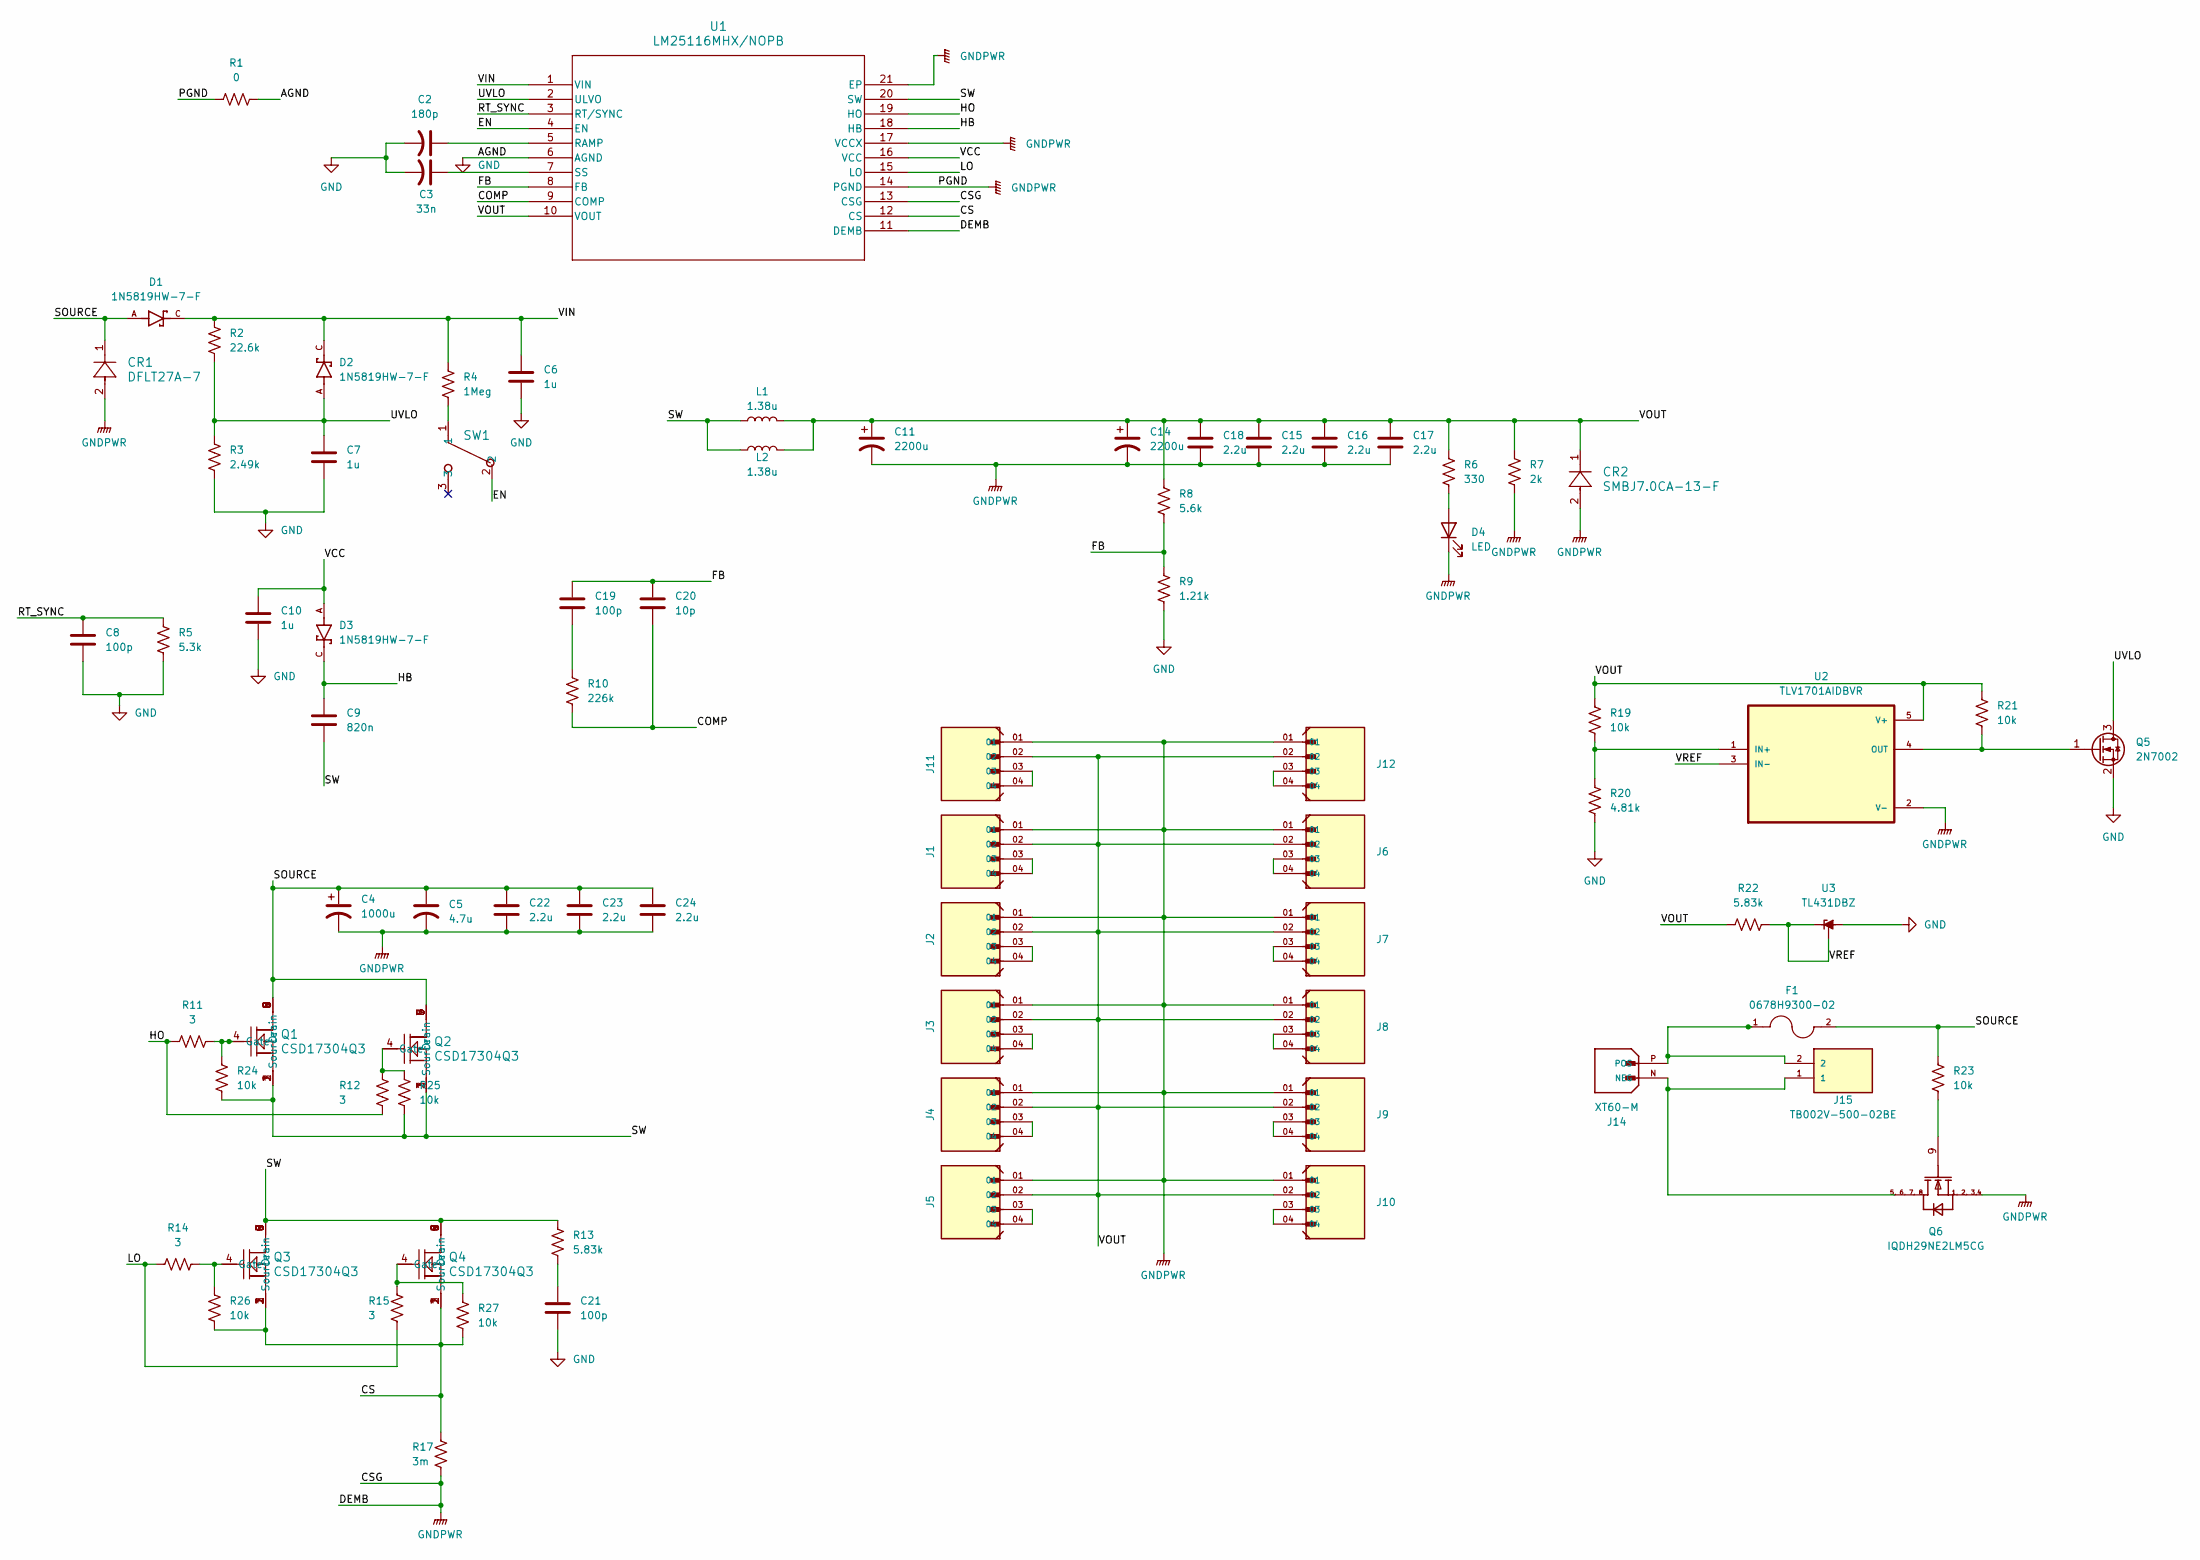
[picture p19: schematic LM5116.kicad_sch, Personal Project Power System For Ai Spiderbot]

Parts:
C2: 180p; C_0603_1608Metric_Pad1.08x0.95mm_HandSolder
C3: 33n; C_1206_3216Metric_Pad1.33x1.80mm_HandSolder
C4: 1000u; CP_Radial_D10.0mm_P5.00mm
C5: 4.7u; C_0805_2012Metric_Pad1.18x1.45mm_HandSolder
C6, C7, C10: 1u; C_0603_1608Metric_Pad1.08x0.95mm_HandSolder
C8, C19, C21: 100p; C_0603_1608Metric_Pad1.08x0.95mm_HandSolder
C9: 820n; C_0603_1608Metric_Pad1.08x0.95mm_HandSolder
C11, C14: 2200u; CP_Radial_D10.0mm_P5.00mm
C15, C16, C17, C18, C22, C23, C24: 2.2u; C_0603_1608Metric_Pad1.08x0.95mm_HandSolder
C20: 10p; C_0603_1608Metric_Pad1.08x0.95mm_HandSolder
CR1: DFLT27A-7; CR_LT27A-7_DIO
CR2: SMBJ7.0CA-13-F; SMB_DIO
D1, D2, D3: 1N5819HW-7-F; SOD3715X145N; PARTREV 18-2
D4: LED; LED_0603_1608Metric_Pad1.05x0.95mm_HandSolder
F1: 0678H9300-02; FUSC9830X318N; PARTREV Dec2019
J1, J2, J3, J4, J5, J6, J7, J8, J9, J10, J11, J12: 61300411121; WURTH_61300411121
J14: XT60-M; AMASS_XT60-M; PARTREV V1.2
J15: TB002V-500-02BE; CUI_TB002V-500-02BE
L1, L2: 1.38u; L_Pulse_PA4341
Q1, Q2, Q3, Q4: CSD17304Q3; DQG0008A
Q5: 2N7002; SOT-23_Handsoldering
Q6: IQDH29NE2LM5CG; IFX-PG-TTFN-9-2-V
R1: 0; R_0402_1005Metric_Pad0.72x0.64mm_HandSolder
R2: 22.6k; R_0805_2012Metric_Pad1.20x1.40mm_HandSolder
R3: 2.49k; R_0805_2012Metric_Pad1.20x1.40mm_HandSolder
R4: 1Meg; R_0402_1005Metric_Pad0.72x0.64mm_HandSolder
R5: 5.3k; R_0603_1608Metric_Pad0.98x0.95mm_HandSolder
R6: 330; R_0603_1608Metric_Pad0.98x0.95mm_HandSolder
R7: 2k; R_0603_1608Metric_Pad0.98x0.95mm_HandSolder
R8: 5.6k; R_0603_1608Metric_Pad0.98x0.95mm_HandSolder
R9: 1.21k; R_0603_1608Metric_Pad0.98x0.95mm_HandSolder
R10: 226k; R_0603_1608Metric_Pad0.98x0.95mm_HandSolder
R11, R12, R14, R15: 3; R_0603_1608Metric_Pad0.98x0.95mm_HandSolder
R13, R22: 5.83k; R_0603_1608Metric_Pad0.98x0.95mm_HandSolder
R17: 3m; R_2512_6332Metric_Pad1.40x3.35mm_HandSolder
R19, R21, R23, R24, R25, R26, R27: 10k; R_0603_1608Metric_Pad0.98x0.95mm_HandSolder
R20: 4.81k; R_0805_2012Metric_Pad1.20x1.40mm_HandSolder
SW1: EG1218; SW_1218_EWI
U1: LM25116MHX/NOPB; MXA20A_TEX-M
U2: TLV1701AIDBVR; SOT95P280X145-5N
U3: TL431DBZ; SOT-23_Handsoldering

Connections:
/COMP: C20.2, R10.2, U1.9 (COMP)
/CS: Q3.1 (Source), Q3.2, Q3.3, Q4.1 (Source), Q4.2, Q4.3, R17.2, R26.1, R27.1, U1.12 (CS)
/FB: C19.1, C20.1, R8.2, R9.1, U1.8 (FB)
/HB: C9.1, D3.C, U1.18 (HB)
/HO: R11.1, R12.2, U1.19 (HO)
/LO: R14.1, R15.1, U1.15 (LO)
/RT_SYNC: C8.1, R5.1, U1.3 (RT/SYNC)
/SOURCE: C4.1, C5.1, C22.1, C23.1, C24.1, CR1.1, D1.A, F1.2, Q1.5 (Drain), Q1.6, Q1.7, Q1.8, Q1.9, Q2.5 (Drain), Q2.6, Q2.7, Q2.8, Q2.9, R23.2
/SW: C9.2, L1.1, L2.1, Q1.1 (Source), Q1.2, Q1.3, Q2.1 (Source), Q2.2, Q2.3, Q3.5 (Drain), Q3.6, Q3.7, Q3.8, Q3.9, Q4.5 (Drain), Q4.6, Q4.7, Q4.8, Q4.9, R13.1, R24.1, R25.1, U1.20 (SW)
/UVLO: C7.1, D2.A, Q5.3 (D), R2.2, R3.1, U1.2 (ULVO)
/VCC: C10.1, D3.A, U1.16 (VCC)
/VIN: C6.1, D1.C, D2.C, R2.1, R4.1, U1.1 (VIN)
/VOUT: C11.1, C14.1, C15.1, C16.1, C17.1, C18.1, CR2.1, J1.02, J2.02, J3.02, J4.02, J5.02, J6.02, J7.02, J8.02, J9.02, J10.02, J11.02, J12.02, L1.2, L2.2, R6.1, R7.1, R8.1, R19.1, R21.1, R22.1, U1.10 (VOUT), U2.5 (V+)
/VREF: R22.2, U2.3 (IN-), U3.1 (K), U3.2 (REF)
GND: C2.2, C3.2, C6.2, C7.2, C8.2, C10.2, C21.2, Q5.2 (S), R1.2, R3.2, R5.2, R9.2, R20.2, SW1.3, U1.6 (AGND), U3.3 (A)
GNDPWR: C4.2, C5.2, C11.2, C14.2, C15.2, C16.2, C17.2, C18.2, C22.2, C23.2, C24.2, CR1.2, CR2.2, D4.1 (K), J1.01, J2.01, J3.01, J4.01, J5.01, J6.01, J7.01, J8.01, J9.01, J10.01, J11.01, J12.01, Q6.1 (SOURCE1), Q6.2 (SOURCE2), Q6.3 (SOURCE3), Q6.4 (SOURCE4), R1.1, R7.2, R17.1, U1.11 (DEMB), U1.13 (CSG), U1.14 (PGND), U1.17 (VCCX), U1.21 (EP), U2.2 (V-)
unnamed: C19.2, R10.1
unnamed: C21.1, R13.2
unnamed: D4.2 (A), R6.2
unnamed: J1.03, J1.04
unnamed: J2.03, J2.04
unnamed: J3.03, J3.04
unnamed: J4.03, J4.04
unnamed: J5.03, J5.04
unnamed: J6.03, J6.04
unnamed: J7.03, J7.04
unnamed: J8.03, J8.04
unnamed: J9.03, J9.04
unnamed: J10.03, J10.04
unnamed: J11.03, J11.04
unnamed: J12.03, J12.04
unnamed: J14.N (NEG), J15.1, Q6.5 (DRAIN1), Q6.6 (DRAIN2), Q6.7 (DRAIN3), Q6.8 (DRAIN4)
unnamed: F1.1, J14.P (POS), J15.2
unnamed: Q1.4 (Gate), R11.2, R24.2
unnamed: Q2.4 (Gate), R12.1, R25.2
unnamed: Q3.4 (Gate), R14.2, R26.2
unnamed: Q4.4 (Gate), R15.2, R27.2
unnamed: Q5.1 (G), R21.2, U2.4 (OUT)
unnamed: Q6.9 (GATE), R23.1
unnamed: C2.1, U1.5 (RAMP)
unnamed: C3.1, U1.7 (SS)
unnamed: R19.2, R20.1, U2.1 (IN+)

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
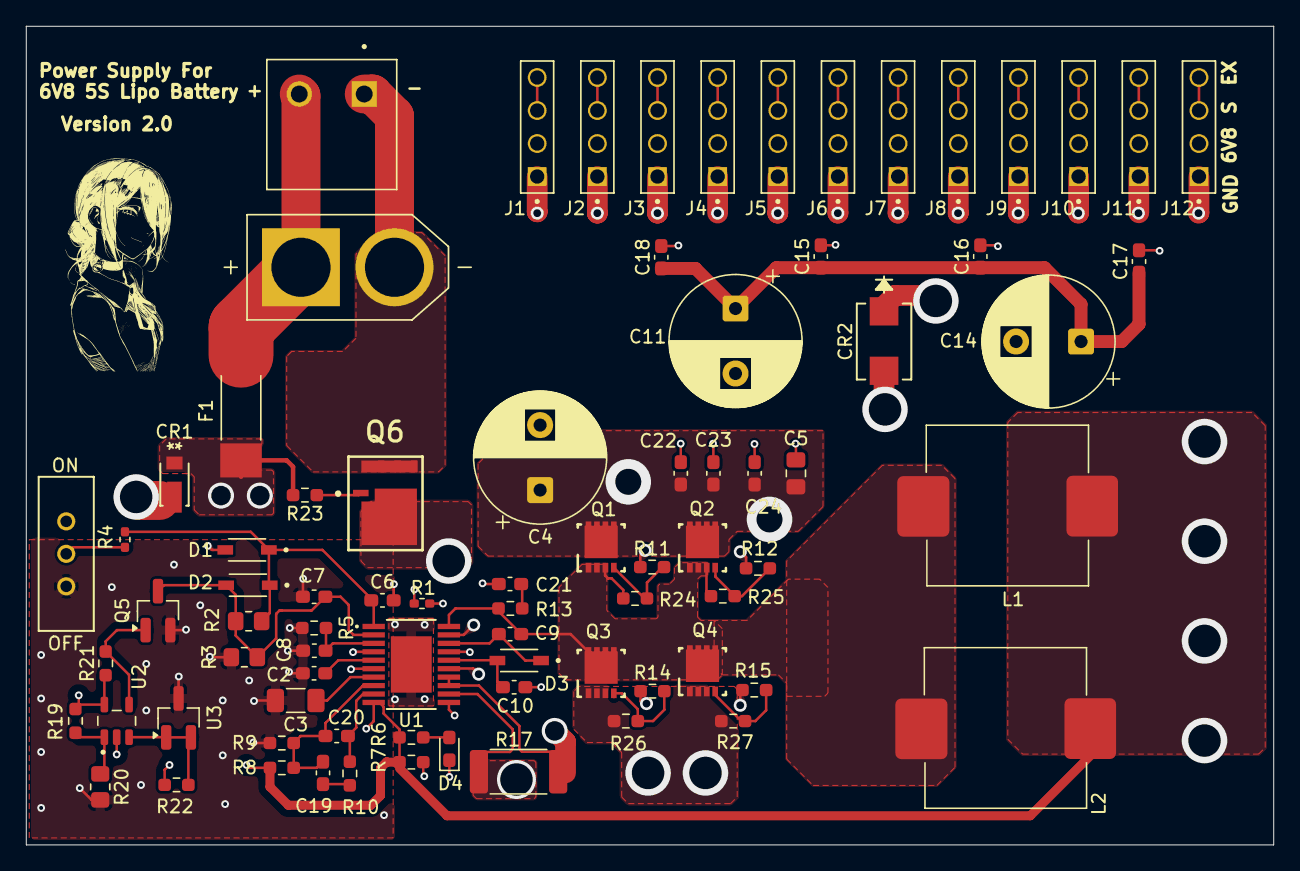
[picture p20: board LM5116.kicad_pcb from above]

Board: 4 copper layers, 96.0 x 63.0 mm, 79 parts (0 on the bottom side), 44 nets.

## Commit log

2026-06-18 Change Name
    [LM5116.dsn]
2026-06-22 Add Component File
    [0678H9300-02.step, TLV1701AIDBVR.step]
2026-06-24 Add Switch
    [100SP1T1B4M2QE.step]
2026-06-26 Add dot for LED
2026-06-26 Initialize README with project details
    Added project description for buck converter design.
2026-06-27 New Kicad File Final
    [LM5116.kicad_pcb, LM5116.kicad_sch]
2026-06-27 Add Kicad File
    [LM5116.kicad_pcb]
2026-06-29 Update Footprint
    [LM5116.kicad_pcb]
2026-06-30 Update Kicad File
    [LM5116-B_Cu.gbr, LM5116-B_Mask.gbr, LM5116-B_Paste.gbr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]
2026-06-30 Update Component List
    [LM5116 Component Buy.xlsx, LM5116 Digikey Component Purchase List.xlsx]
2026-06-30 Update buck converter specifications in README
2026-06-30 Update Adding pulldown resistor
    [LM5116.kicad_pcb, LM5116.kicad_sch]
